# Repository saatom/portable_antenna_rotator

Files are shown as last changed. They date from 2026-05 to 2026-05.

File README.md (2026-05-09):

# Portable Antenna Rotator
Made by two teams as part of our senior design capstone projects for our respective degrees at the University of Alaska Fairbanks
| Mechanical Engineering | Electrical Engineering |
|---|---|
| Alex Armstrong | Nadia Finley |
| Matthew Crisafi-Lurtsema | Isaac Newton |
| [Wyatt Richards](mailto:wr1701@proton.me) | William Payne |

## Overview
This project was made for the Arctic Amateur Radio Club (KL7KC) in Fairbanks, Alaska to enable easy radio communication with satellites and ground-based targets alike with a single, GPS-enabled device with 400+ degrees of azimuth and 180 degrees of elevation control.

The code is intended to be run on a Raspberry Pi 4b with the relevant Python packages installed.
antenna_pic

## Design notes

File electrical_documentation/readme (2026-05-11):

# The electrical_documentation folder holds an interface control document (ICD) and drawing files that describe the electrical connections 
# for the portable antenna rotator.

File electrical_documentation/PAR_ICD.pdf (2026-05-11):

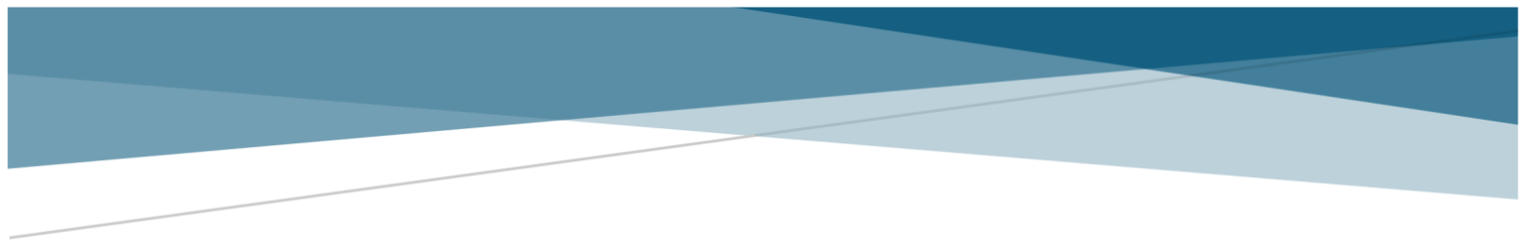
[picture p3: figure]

# PORTABLE ANTENNA ROTATOR (PAR)

## Interface Control Document

Version 1.0
04/29/2026

University of Alaska Fairbanks | EE 482 Senior Design

i
ICD Version 1.0 | Portable Antenna Rotator

## Contents

ii

## Table of Figures

iii

## List of Tables

## 1. Introduction

This ICD describes the relationship between:
- PAR electrical box and the PAR rotator structure.
- PAR electrical box and the external power source.
- Raspberry Pi 4B (RPi) and the connected sensors, motors, touchscreen, and relays.
- PAR and the operator.

This ICD specifies the interface requirements which the participating systems must meet. It describes the concept of operations for the interface, defines the protocols that govern the interchange of data, and identifies the communication paths along which the project team expects signals to flow.
For each interface, the ICD provides the following information:
- A description of the data exchange format and protocol for exchange
- A general description of the interface
- Assumptions where appropriate

## 1.1 Overview

The interface between the electrical box and the rotator structure exists to convey power and control signals between the rotator structure and the electrical box. A 10 ft DSUB cable provides power for the motors, control signals for the motors, I2C signals for the magnetometer / accelerometer, and analog voltages from the potentiometer on the rotator structure.
The interface between the electrical box and the external power source exists to provide a way to power PAR and distribute power to additional equipment. An Anderson power pole bus connected to the outer wall of the electrical box provides a way for the operator to connect a battery. Additional equipment may also be connected to this bus to receive power from the battery.
The interface between the RPi and the connected sensors, motors, touchscreen, and relays exists to provide the RPi with data about the condition of the electrical box and its surroundings, steer the rotator structure in a desired direction, and control indication lights. Dupont connectors link RPi GPIO pins to voltage buses and pin connections on the sensors. The interface between PAR and the operator exists to provide a way for the operator to input data, see RPi operation, manage files, analyze satellite passes, and control the rotator structure.

## 2. Assumptions/Constraints/Risks

It is assumed that the operator will provide their own power through a power pole connection.

## 2.2 Constraints

Connection to the rotator structure must be done with the provided 17 pin DSUB cable. This cable must only be connected to the PAR electrical box to avoid damaging components as the motors will draw significant current.
The power source connected to the power pole bus must have a voltage within 9 – 32 VDC. Whenever voltage from the source degrades below 9 VDC, the system will lose power. The operator should take this into consideration when connecting a battery.

## 3. Interface Overview

## 3.1 Interface Overview

The electrical box-rotator structure interface conveys power and control signals between the electrical box and the rotator structure. The interface is made through a 17-pin, 10 ft DSUB cable. This cable provides 12 VDC power for the elevation servo motor, 5 VDC for the azimuth control feedback potentiometer, and 3 VDC for an accelerometer. Alongside power distribution, the DSUB cable also relays I2C data between the accelerometer and the RPi, analog data from the potentiometer to an analog to digital converter in the electrical box, PWM signals from the RPi to the servo motor, and pulse control signals to the azimuth stepper motor from the stepper motor driver.
The interface between the electrical box and the external power source provides a way to power the Portable Antenna Rotator (PAR) and distribute power to additional equipment. The interface is made through a six-pole, twelve terminal power pole bus that is connected to the outer wall of the electrical box. This bus allows the operator to connect a battery through the power pole connectors. Allowable voltages on this bus are 9 VDC to 32 VDC. Power from the power pole connection is distributed to both the control / operator interface circuitry inside the electrical box as well as to the motors and electrical components on the rotator structure. Additional equipment separate from PAR can be powered from the power pole bus by connecting the equipment in parallel to the battery.

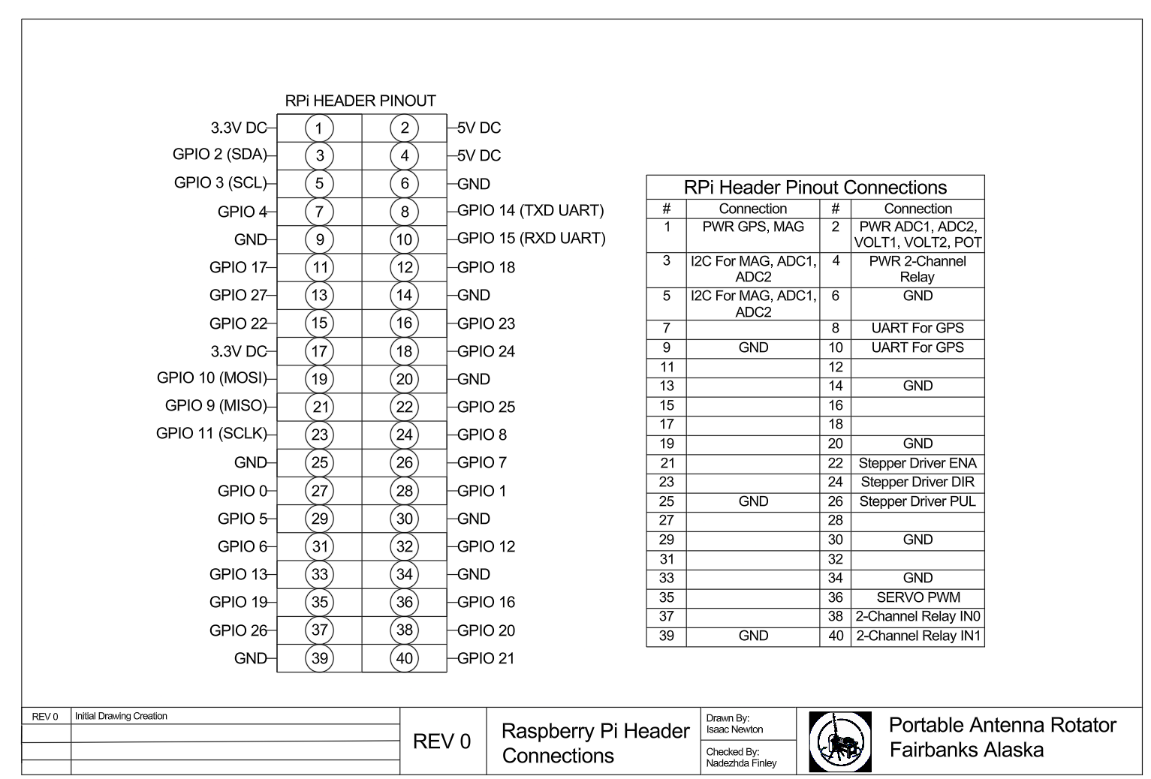
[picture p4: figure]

Figure 1: PAR-004 Design Drawing, RPi Header Diagram

The interface between the RPi and the sensors, motors, touchscreen, and relays provides the RPi a way to perceive information about PAR and its surroundings, control the rotator structure, and communicate system information to the operator. The RPi DSI FPC display port is used to connect the RPi to the touchscreen display, and the RPi 40-pin GPIO is used to connect the RPi to the various peripherals. Figure 1 above shows connections on the RPi GPIO for reference. Signal interfacing protocols on the GPIO include I2C, UART, PWM, and pulse signals written into the Portable Antenna Rotator Router (PARR) program. +3 VDC and +5 VDC power for low current draw sensors are also sourced from the RPi GPIO. Devices connected to the RPi include: two USB extension cables, a 7 inch touchscreen display, two analog to digital converters, two voltage divider “voltmeters”, a GPS, an accelerometer / magnetometer, a servo motor, a stepper motor driver, and a relay for the LED indication lights. Dupont connectors link RPi GPIO pins to voltage buses and pin connections on the sensors.
The interface between PAR and the operator provides a way for the operator to input data, visualize RPi operation, manage files, interact with satellite tracking software, and control the rotator structure. The interface is accomplished through a touch screen, two accessible USB-A ports, a power switch, and an emergency power-off button. The touchscreen provides a way for the operator to interact with the PARR program, communicate with the controller, and steer the rotator structure. The USB-A ports allow the operator to connect a USB storage device, mouse, or keyboard to the RPi for file upload and interfacing. The power switch and emergency power-off button allow the operator to control the flow of power to PAR. The switch connects and disconnects power from the power pole bus to PAR, and the emergency power-off button is a resettable button that disconnects power from the RPi and motors and turns on a green LED light while compressed.

3.1.1 Interface Controls

Table 1: Electrical Box to Rotator Structure Interface Connections
Interface Type | Interface From | Interface To | Description of Interface | Other Information
DSUB Connector | PAR rotator structure | PAR electrical box | Connects 12 VDC power, 5 VDC power, 3 VDC power, stepper motor control signals, PWM signals, I2C signals, and analog potentiometer voltage between the rotator structure and RPi

Table 2: Electrical Box to External Power Source Interface Connections
Interface Type | Interface From | Interface To | Description of Interface | Other Information
9 - 32 VDC power | Power source | Electrical box | Anderson Power Pole Connectors

Table 3: RPi to Sensors, Motors, Touchscreen, and Relay Interface Connections
Interface Type | Interface From | Interface To | Description of Interface | Other Information
RPi GPIO | Board Pin # 1 | Magnetometer, GPS | 3.3 VDC Power
RPi GPIO | Board Pin # 2 | ADC1, ADC2, Voltmeter1, Voltmeter2, Potentiometer | 5 VDC Power

RPi GPIO | Board Pin # 3 | Magnetometer / Accelerometer, ADC1, ADC2 | SDA
RPi GPIO | Board Pin # 4 | 2CH Relay (LED) | 5 VDC Power
RPi GPIO | Board Pin # 5 | Magnetometer / Accelerometer, ADC1, ADC2 | SCL
RPi GPIO | Board Pin # 6 | GND | GND
RPi GPIO | Board Pin # 9 | GND | GND
RPi GPIO | Board Pin # 8 | GPS RX | UART (RPi TX)
RPi GPIO | Board Pin # 10 | GPS TX | UART (RPi RX)
RPi GPIO | Board Pin # 14 | GND | GND
RPi GPIO | Board Pin # 20 | GND | GND
RPi GPIO | Board Pin # 22 | Stepper Motor Driver | Stepper Enable
RPi GPIO | Board Pin # 24 | Stepper Motor Driver | Stepper Direction
RPi GPIO | Board Pin # 25 | GND | GND
RPi GPIO | Board Pin # 26 | Stepper Motor Driver | Stepper Pulse
RPi GPIO | Board Pin # 30 | GND | GND
RPi GPIO | Board Pin # 34 | GND | GND
RPi GPIO | Board Pin # 36 | Servo Motor | PWM Signal
RPi GPIO | Board Pin # 38 | 2CH Relay (LED) | Pulse Signal
RPi GPIO | Board Pin # 39 | GND | GND
RPi GPIO | Board Pin # 40 | 2CH Relay (LED) | Pulse Signal
RPi USB | RPi USB-A | USB Extension Cable
RPi USB | RPi USB-A | USB Extension Cable
RPi Display Port | RPi DSI Display Port | 7 Inch Touchscreen Display | FPC Connector

Figure 2 shows a KiCad schematic for the connections to the RPI GPIO.

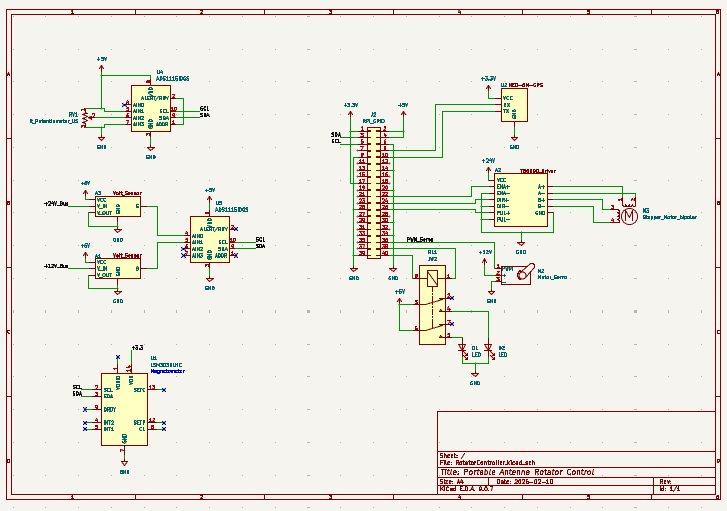
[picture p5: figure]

Figure 2: Portable Antenna Rotator RPi GPIO Connections, KiCad Schematic

Table 4: PAR Electrical Box to Operator Interface Connections
Interface Type | Interface From | Interface To | Description of Interface | Other Information
Touchscreen | Touchscreen | Operator | Provides the Operator with Visual Feedback and Tactile Control of the RPi
USB Port 1 | RPi USB Port | External USB-A Connector
USB Port 2 | RPi USB Port | External USB-A Connector
Power Switch | Power Line | Operator | Allows Operator to Control Power Flow to PAR
Emergency Power-off Button | Further Along the Power Line | Operator | Allows Operator to Remove and Restore Power to the RPi and Motors

## 3.2 Functional Allocation

The function of the electrical box is to act as the control and power distribution center of PAR. The DSUB interface between the electrical box and the rotator structure supports the function of the electrical box by transmitting power and signals to components on the rotator structure. To engage the DSUB interface, the operator must uncoil the 10 ft cable from stowed position and plug the cable into the DSUB terminal on the electrical box.
The function of the electrical box to external power source interface is to provide a way for the operator to connect power to the PAR system and other devices connected to the power pole bus. To connect a power source to the power pole bus, the operator must connect cables terminated with Anderson power pole connectors to the power pole bus on the box. To power external devices off of the power pole bus, the operator must plug in devices to the bus using cables terminated with Anderson power pole connectors.

The function of the RPi to sensors and motors interface is to provide the RPi with a means of sensing its surroundings and to control the rotator structure. There is nothing that the operator must do to engage this interface for system operation.
The function of the PAR to operator interface is to provide a way for the operator to engage with the PAR system. To power on PAR, the operator will need to disengage the emergency power-off button and flip the power switch to the “ON” position. To navigate files, apps, and the PARR program, the operator must either utilize the touchscreen function of the display or connect a mouse and keyboard to the USB ports.

## Appendix A: Record of Changes

This interface control document should be kept in a folder with other PAR related documentation to keep a record of interface connections and purposes for system maintenance and updates to system design.

Table 5: Record of Changes

Version Number | Date | Author | Description of Change
1.1 | 04/29/2026 | Nadezhda Finley | First version; no changes
<X.X> | <MM/DD/YYYY> | | <Description of Change>
<X.X> | <MM/DD/YYYY> | | <Description of Change>
<X.X> | <MM/DD/YYYY> | | <Description of Change>

## Appendix B: Glossary

Table 6: Glossary
Term | Acronym | Definition
Portable Antenna Rotator | PAR | The portable antenna rotator is the antenna rotator system whose interfaces are described in the present document. PAR consists of an electrical box and a rotator structure.
Portable Antenna Rotator Router | PARR | Portable Antenna Rotator Router is the Python software program written to control PAR.

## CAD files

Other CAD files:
electrical_documentation/electrical_drawings/Rpi_Header.dwg
electrical_documentation/electrical_drawings/One_Line.dwg
electrical_documentation/electrical_drawings/Electrical_Box.dwg
electrical_documentation/electrical_drawings/DC-Schematic_2.dwg
electrical_documentation/electrical_drawings/D-Sub Connector.dwg

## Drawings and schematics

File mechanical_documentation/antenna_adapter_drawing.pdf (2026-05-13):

# 98.15 mm

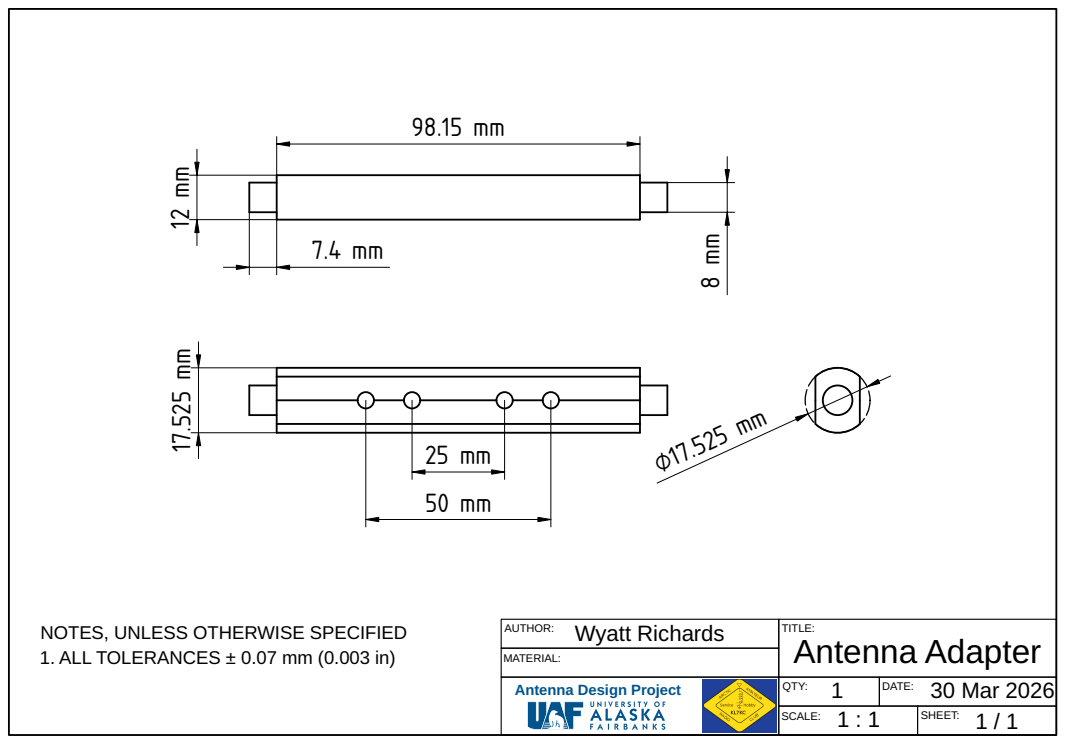
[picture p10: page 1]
AUTHOR:; DATE:; SHEET:; SCALE:; TITLE:; Wyatt Richards; 30 Mar 2026; 1. ALL TOLERANCES ± 0.07 mm (0.003 in); Antenna Adapter; QTY:

NOTES, UNLESS OTHERWISE SPECIFIED

MATERIAL:
Antenna Design Project

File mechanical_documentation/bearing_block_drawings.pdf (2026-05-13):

0.188 "

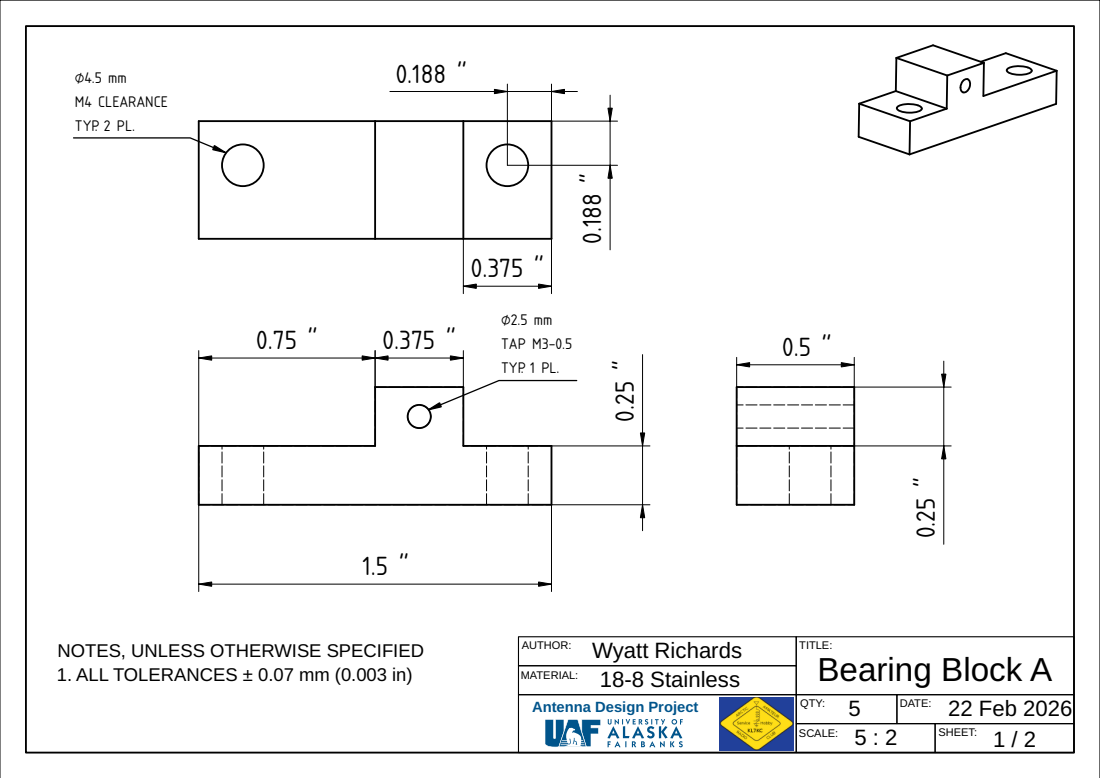
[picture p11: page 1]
AUTHOR:; DATE:; SHEET:; SCALE:; TITLE:; MATERIAL:; Wyatt Richards 18-8 Stainless; 22 Feb 2026; 1. ALL TOLERANCES ± 0.07 mm (0.003 in); Bearing Block A; QTY:; TAP M3-0.5; TYP. 1 PL.; M4 CLEARANCE; TYP. 2 PL.

NOTES, UNLESS OTHERWISE SPECIFIED

Antenna Design Project

⌀0.118 "

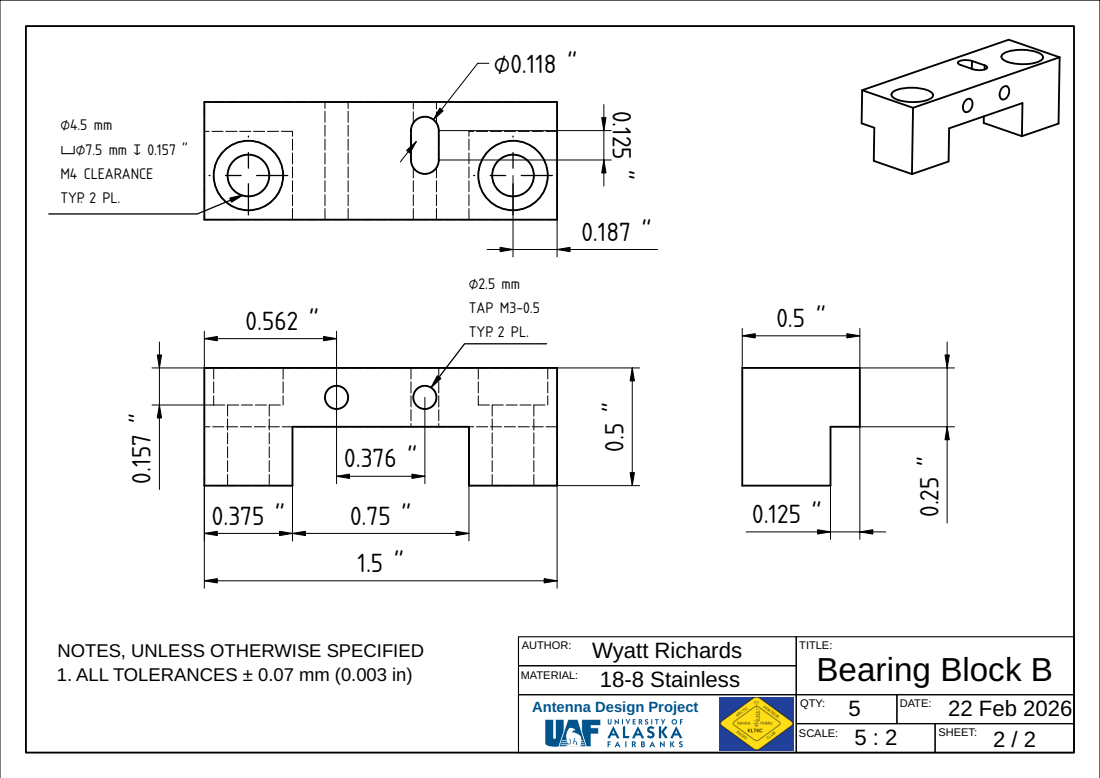
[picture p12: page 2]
AUTHOR:; DATE:; SHEET:; SCALE:; TITLE:; MATERIAL:; Wyatt Richards 18-8 Stainless; 22 Feb 2026; 1. ALL TOLERANCES ± 0.07 mm (0.003 in); Bearing Block B; QTY:; TAP M3-0.5; TYP. 2 PL.; M4 CLEARANCE

NOTES, UNLESS OTHERWISE SPECIFIED

Antenna Design Project

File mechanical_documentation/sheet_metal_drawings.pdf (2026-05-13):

205.41 mm

## 38.1 mm ⌀4.5 mm

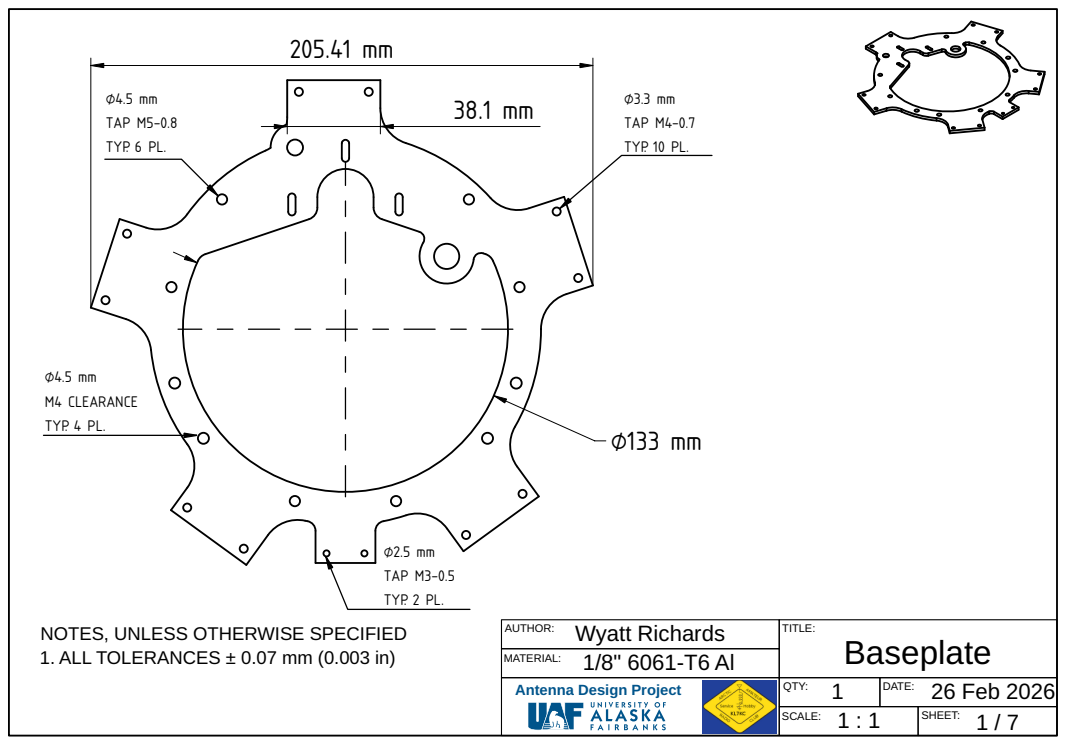
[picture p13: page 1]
AUTHOR:; DATE:; SHEET:; SCALE:; TITLE:; MATERIAL:; Wyatt Richards 1/8" 6061-T6 Al; 26 Feb 2026; 1. ALL TOLERANCES ± 0.07 mm (0.003 in); Baseplate; QTY:; TAP M5-0.8; TYP. 6 PL.; TAP M4-0.7; TYP. 10 PL.; M4 CLEARANCE; TYP. 4 PL.; TAP M3-0.5; TYP. 2 PL.

NOTES, UNLESS OTHERWISE SPECIFIED

Antenna Design Project

138 mm

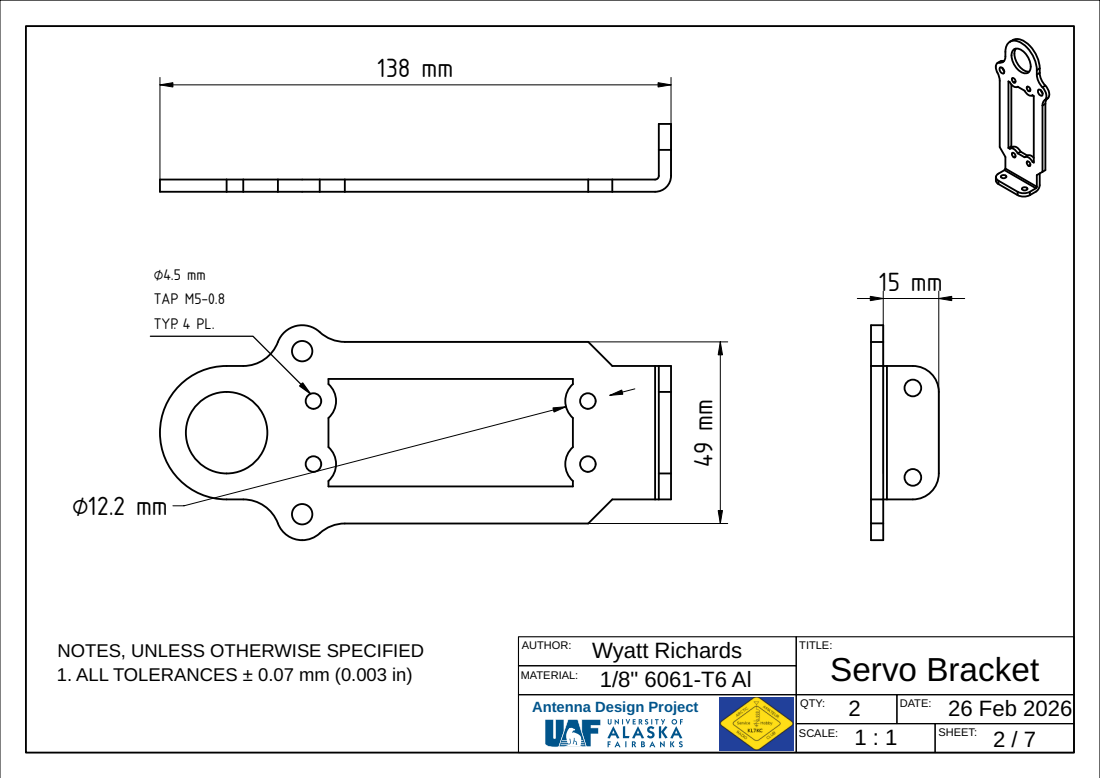
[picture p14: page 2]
AUTHOR:; DATE:; TITLE:; MATERIAL:; Wyatt Richards 1/8" 6061-T6 Al; 26 Feb 2026; 1. ALL TOLERANCES ± 0.07 mm (0.003 in); Servo Bracket; QTY:; TAP M5-0.8; TYP. 4 PL.

NOTES, UNLESS OTHERWISE SPECIFIED

Antenna Design Project

## R14 mm

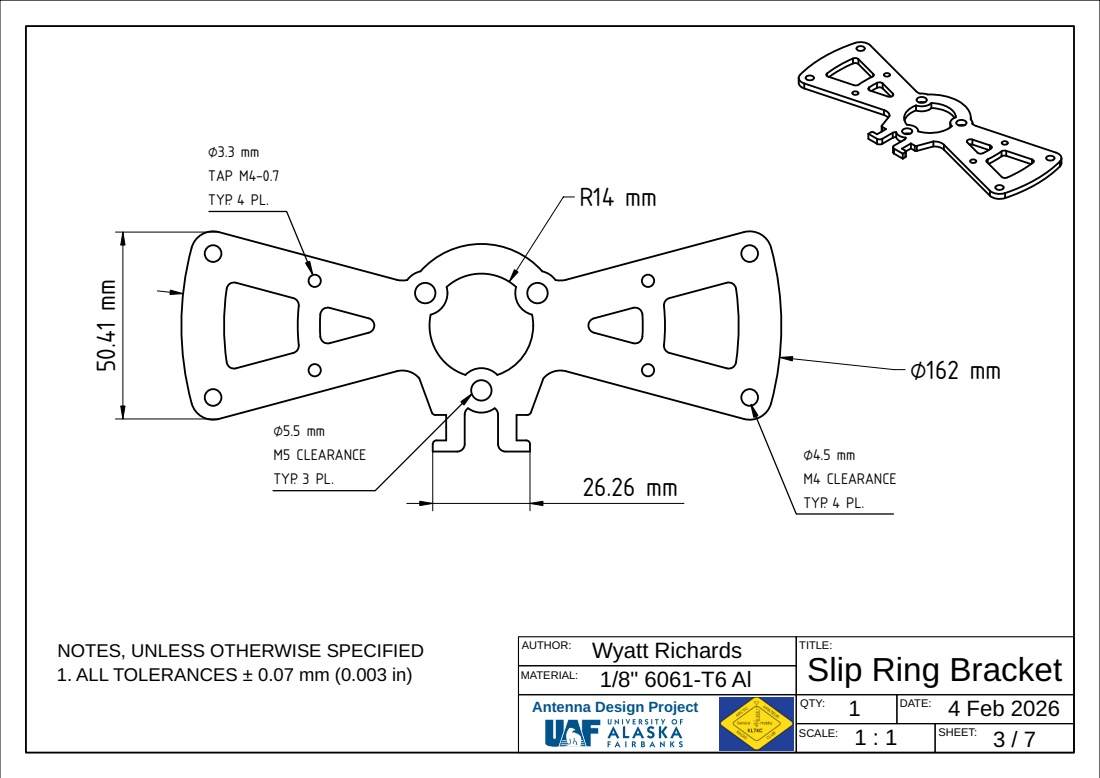
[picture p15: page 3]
AUTHOR:; DATE:; TITLE:; MATERIAL:; Wyatt Richards 1/8" 6061-T6 Al; 4 Feb 2026; 1. ALL TOLERANCES ± 0.07 mm (0.003 in); Slip Ring Bracket; QTY:; TAP M4-0.7; TYP. 4 PL.; M4 CLEARANCE; M5 CLEARANCE; TYP. 3 PL.

NOTES, UNLESS OTHERWISE SPECIFIED

Antenna Design Project

59.11 mm

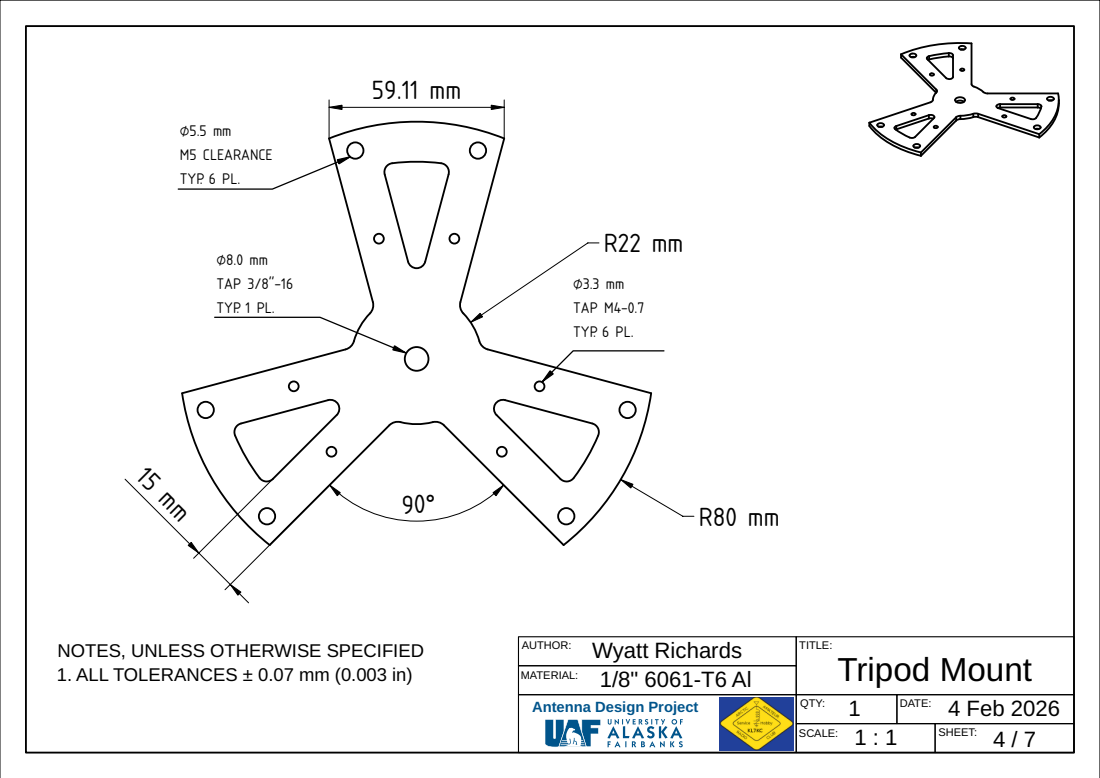
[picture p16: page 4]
AUTHOR:; DATE:; TITLE:; MATERIAL:; Wyatt Richards 1/8" 6061-T6 Al; 4 Feb 2026; 1. ALL TOLERANCES ± 0.07 mm (0.003 in); Tripod Mount; QTY:; TAP M4-0.7; TYP. 6 PL.; M5 CLEARANCE; TAP 3/8"-16; TYP. 1 PL.

NOTES, UNLESS OTHERWISE SPECIFIED

Antenna Design Project

⌀3.3 mm

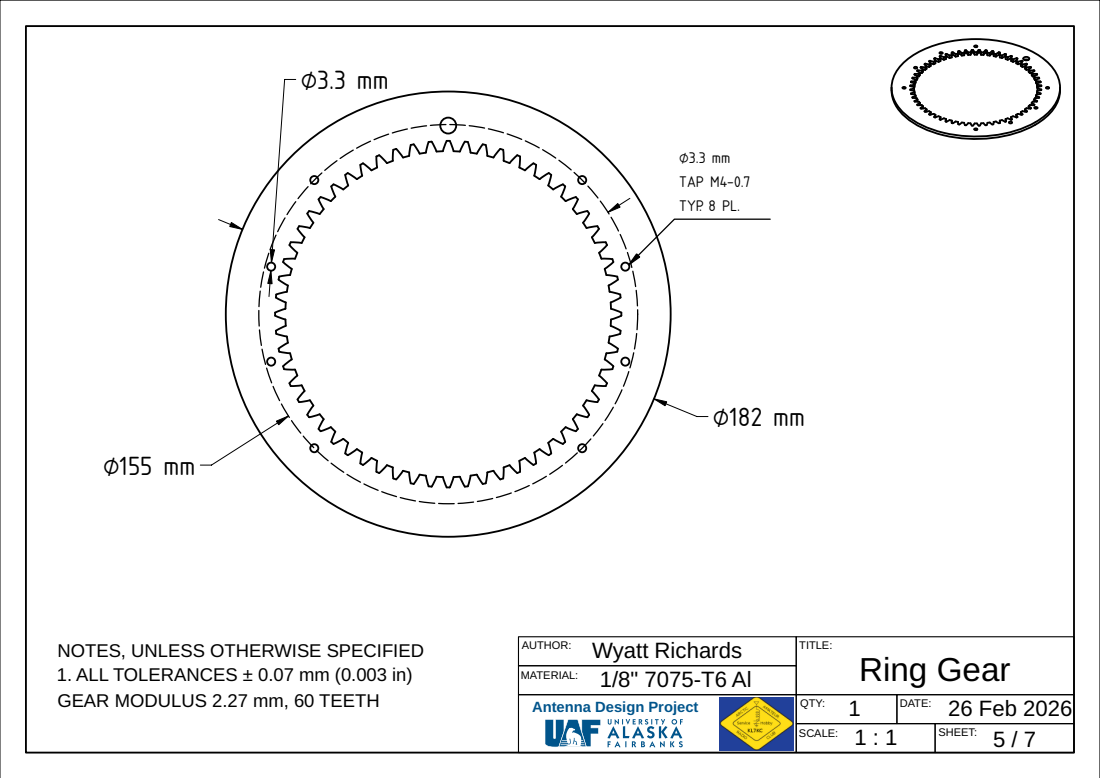
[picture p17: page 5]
AUTHOR:; DATE:; TITLE:; MATERIAL:; Wyatt Richards 1/8" 7075-T6 Al; 26 Feb 2026; 1. ALL TOLERANCES ± 0.07 mm (0.003 in); Ring Gear; GEAR MODULUS 2.27 mm, 60 TEETH; QTY:; TAP M4-0.7; TYP. 8 PL.

NOTES, UNLESS OTHERWISE SPECIFIED

Antenna Design Project

⌀17.52 mm

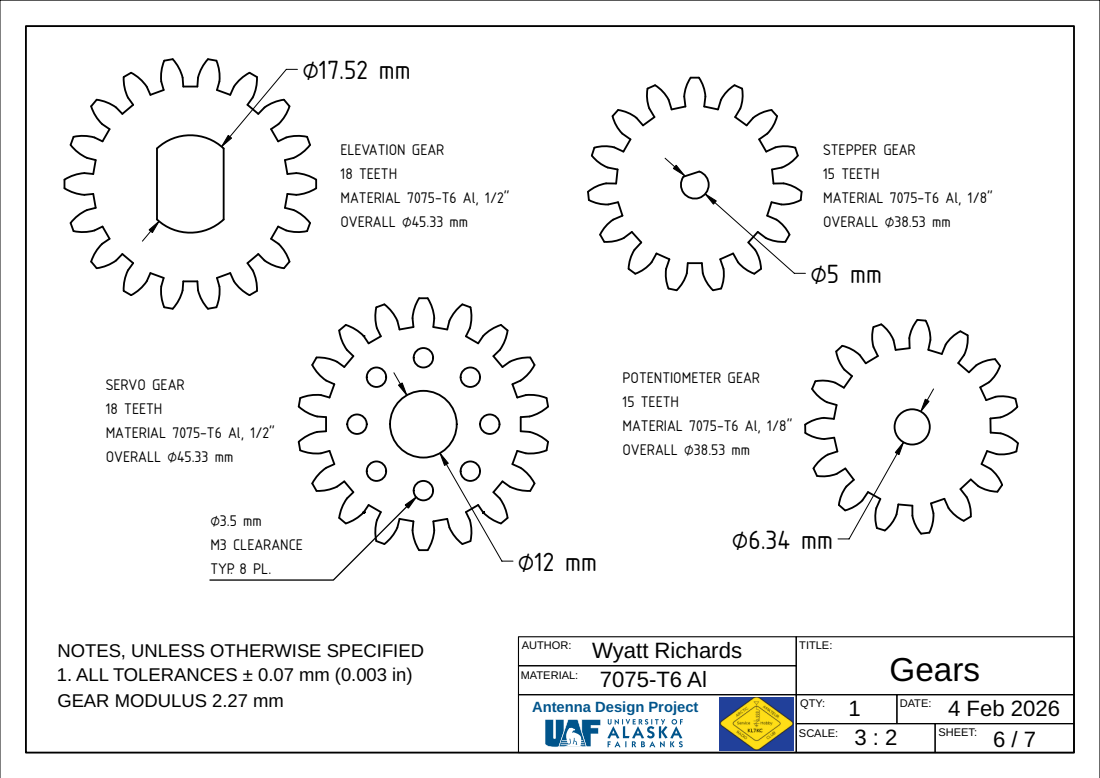
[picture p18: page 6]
AUTHOR:; DATE:; TITLE:; MATERIAL:; Wyatt Richards 7075-T6 Al; 4 Feb 2026; 1. ALL TOLERANCES ± 0.07 mm (0.003 in); Gears; GEAR MODULUS 2.27 mm; QTY:; ELEVATION GEAR; 18 TEETH; MATERIAL 7075-T6 Al, 1/2"; OVERALL ⌀45.33 mm; SERVO GEAR; STEPPER GEAR; 15 TEETH; MATERIAL 7075-T6 Al, 1/8"; OVERALL ⌀38.53 mm; POTENTIOMETER GEAR; M3 CLEARANCE; TYP. 8 PL.

NOTES, UNLESS OTHERWISE SPECIFIED

Antenna Design Project

3.3 mm

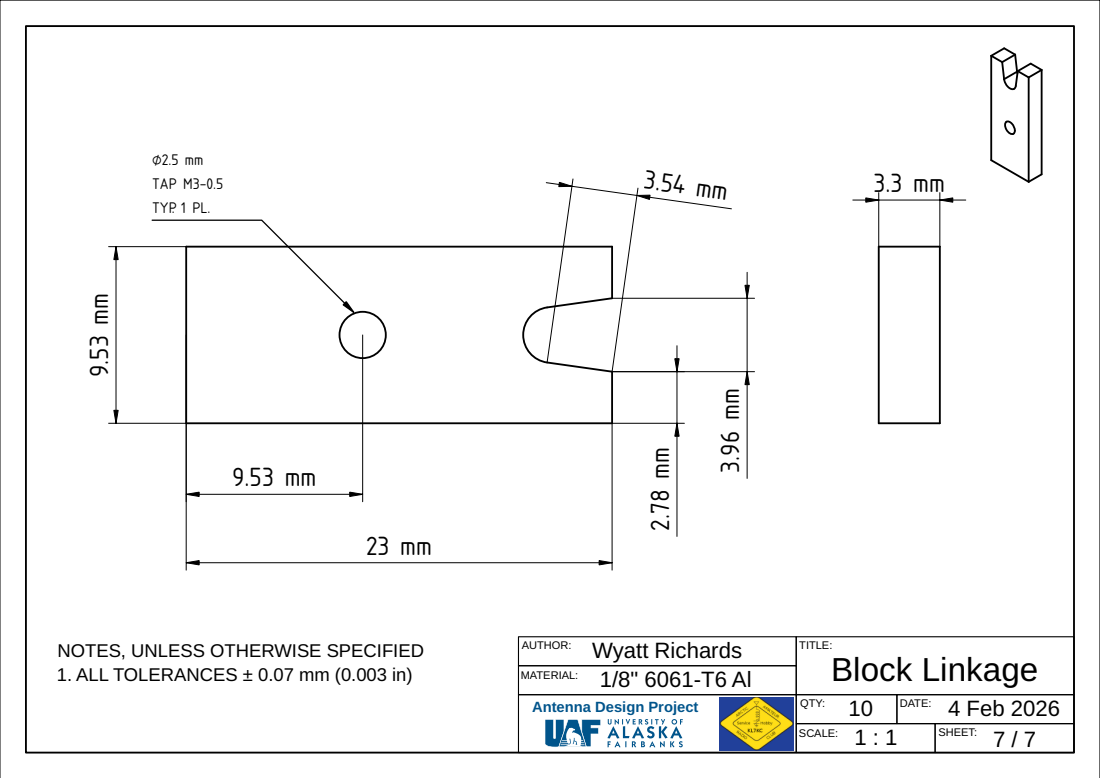
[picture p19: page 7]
AUTHOR:; DATE:; TITLE:; MATERIAL:; Wyatt Richards 1/8" 6061-T6 Al; 4 Feb 2026; 1. ALL TOLERANCES ± 0.07 mm (0.003 in); Block Linkage; QTY:; TAP M3-0.5; TYP. 1 PL.

NOTES, UNLESS OTHERWISE SPECIFIED

Antenna Design Project

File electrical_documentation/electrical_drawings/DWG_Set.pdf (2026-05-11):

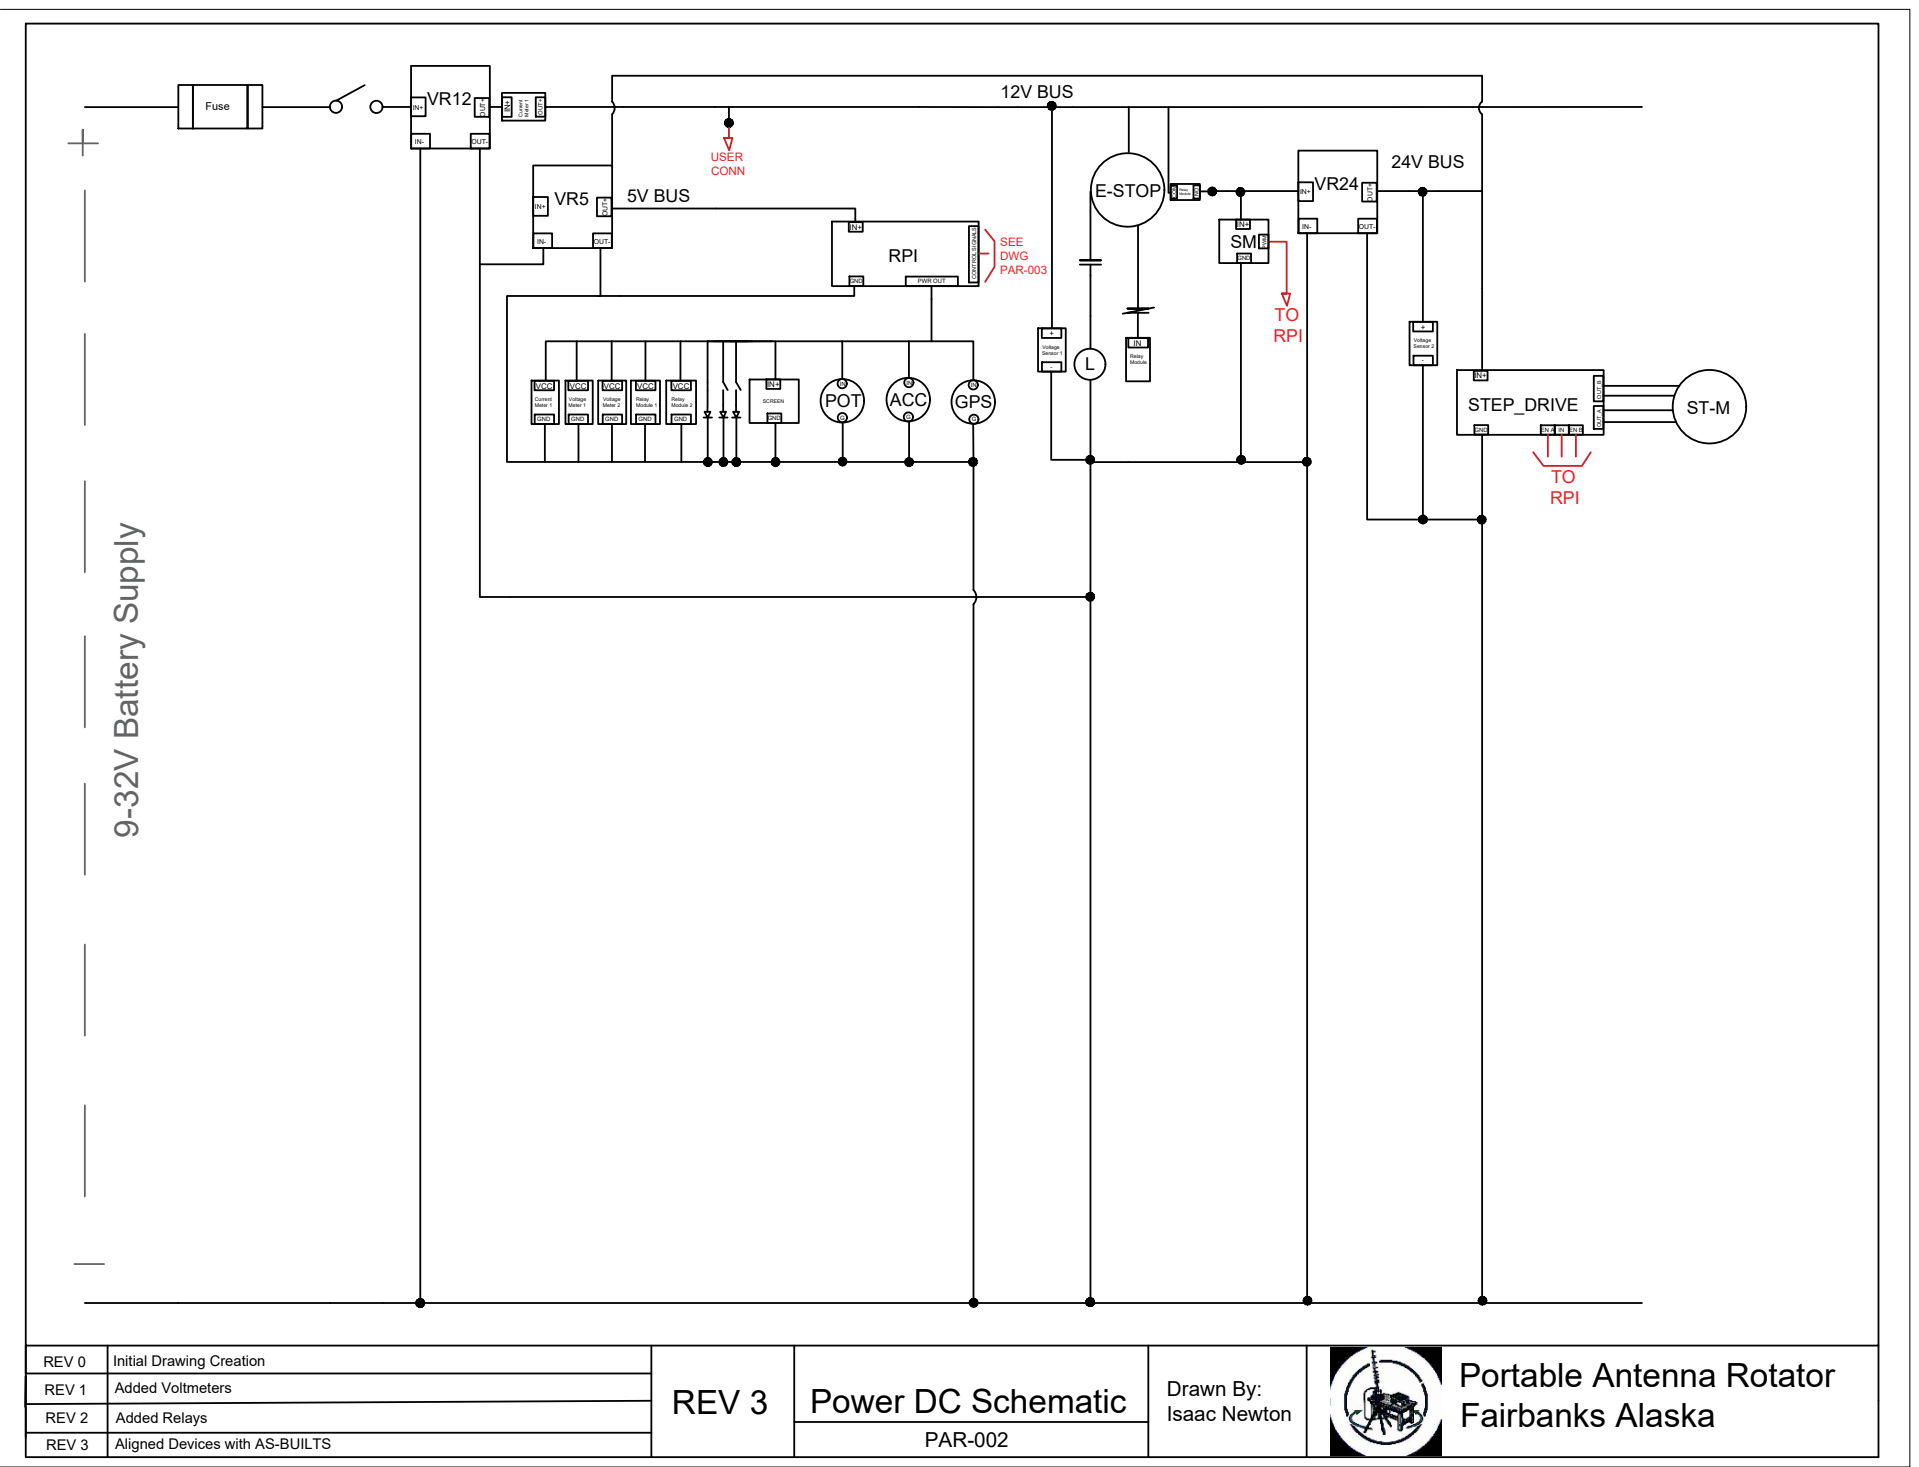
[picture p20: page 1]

9-32V Battery Supply Fuse IN+IN- OUT+ OUT- VR12 12V BUS E-STOP L SMIN+ GND IN+IN- OUT+ OUT- VR24 24V BUS

Current Meter 1 OUT+ Portable Antenna Rotator Fairbanks Alaska Drawn By: REV 3 Power DC Schematic Isaac Newton REV 0 REV 1 REV 2 REV 3 Initial Drawing Creation Added Voltmeters Added Relays Aligned Devices with AS-BUILTS PAR-002

CONTROL SIGNALS PWR OUT SCREEN POT ACC GPS IN+ GND G G G IN IN IN SEE DWG PAR-003 USER CONN VCC GND Voltage Meter 1 VCC GND Voltage Meter 2 +- Voltage Sensor 1 +- Voltage Sensor 2 INRelay Module

COMRelay Module NO VCC GND Relay Module 1 VCC GND Relay Module 2 VCC GND Current Meter 1

OUT_B OUT_AST-M EN A IN EN B TORPI IN+IN- OUT+ OUT- VR5 5V BUS RPI IN+ GND

PWM TORPI STEP_DRIVE IN+ GND

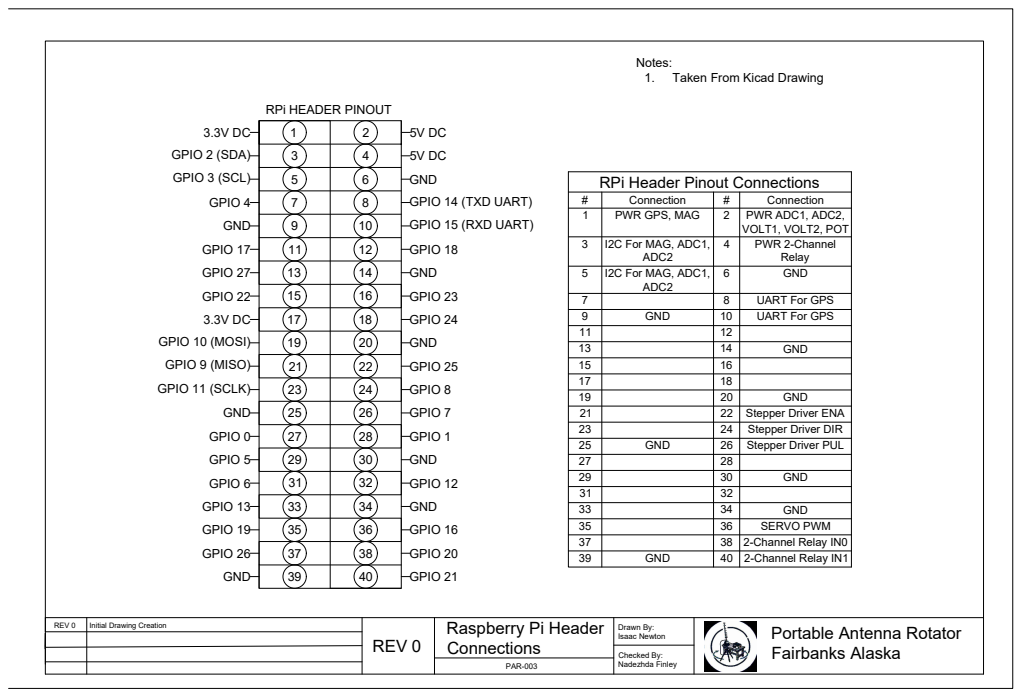
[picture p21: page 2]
Portable Antenna Rotator Fairbanks Alaska Drawn By: Isaac Newton Checked By: Nadezhda Finley Raspberry Pi Header REV 0; Connections REV 0; Initial Drawing Creation; 5V DC 5V DC GND GPIO 14 (TXD UART) GPIO 15 (RXD UART) GPIO 18 GND GPIO 23 GPIO 24 GND GPIO 25 GPIO 8 GPIO 7 GPIO 1 GND GPIO 12 GND GPIO 16 GPIO 20 GPIO 21 3.3V DC GPIO 2 (SDA) GPIO 3 (SCL) GPIO 4 GND GPIO 17 GPIO 27 GPIO 22 3.3V DC GPIO 10 (MOSI) GPIO 9 (MISO) GPIO 11 (SCLK) GND GPIO 0 GPIO 5 GPIO 6 GPIO 13 GPIO 19 GPIO 26 GND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

2 1:SERVO PWR 2:SERVO GND 3:MAG PWR 4:MAG SDA 5:MAG SDL; 6:MAG GND 7:POT + 8:POT SLIDE 9:POT - 10:SERVO SIG 11:SPARE 12:A+ 13:A- 14:B+ 15:B-; 16:SPARE 17:SPARE 9; 1 1:SERVO PWR 2:SERVO GND 3:MAG PWR 4:MAG SDA 5:MAG SDL; 16:SPARE 17:SPARE FEMALE SIDE REAR VIEW MALE SIDE REAR VIEW; Portable Antenna Rotator Fairbanks Alaska Drawn By: Isaac Newton D-Sub Layout REV 1 REV 0 REV 1; Initial Drawing Creation Added Servo Signal Connection; PAR-004

LEFT SIDE

CONTROL SIGNALS 3.3V PWR OUT Screen IN+ GND GPSGIN IN: AE-OUT+, AE-OUT- GND: AD-GND, AM-GND, ADC1-GND, ADC2-GND 3.3V: ACC-IN 5V: AD-VCC, AM-IN+, AM-IN+,ADC1-VCC,ADC2-VCC,POT-IN SDA: ADC1-SDA,ADC2-SDA,ACC-SDA SCL: ADC1-SCL,ADC2-SCL,ACC-SCL TX: RX: IN+: AK-5V GND: AK-GND AB-OUT+ IN: ACC-IN, L1-IN G: AK-GND AE-IN+ POTGIN IN: AK-5V SLIDE: ADC2-A2 G: AK-GND --AG-- OUT-VR24 OUT+ IN- IN+: T1-8 IN-:T2-5 OUT+: T1-9 OUT-: T2-7 IN+ AA Current meter 1 IN+ VCC IN+: OUT+: VCC: SIG: GND: OUT+ SIG GND AB AD Volt meter 1 + VCC +: T1-5 -: T2-4 VCC: AD-VCC, AG-VCC SIG: ADC1-A1 GND: AK-GND - SIG GND AF Volt meter 2 VCC +: T1-9 -: T2-7 VCC: AF-VCC, AH-VCC SIG: ADC1-A0 GND: AK-GND SIG GND AG Relay 1 VCC NO1: L2-IN COM1: L1-IN NC1: NO2: L3-IN COM2: AH-COM1 NC2: VCC: AG-VCC, AI-DC+ IN1: IN2: GND: AK-GND IN1 IN2 AH Relay 2 DC+ NO: COM: T1-8 NC: DC+: AH-VCC DC-: AK-GND IN: AC-NC2 DC- IN AI AE + - NO COM NC NO COM NC NO COM NC K1 K2 GND AC-NO1 AB-IN+ VM 1 ESTOP ESTOP 24V IN NO2 NC2 ESTOP NO1 NC1 AJ AL N/A 24V OUT STEP-DR AK AM L2 IN: AH-NO1 GND: L1-GND, L3-GND L3 IN: AH-NO2 GND: L2-GND, T2-3 L4 IN: AC-NO2 GND: T2-4 AE-IN- L3-GND L4-GND AB-IN- AA-OUT- AB-OUT- AL-GND BOX LEVEL 2 P1-7 ACCGIN IN: AK-3.3V G: AK-GND Portable Antenna Rotator Fairbanks Alaska Drawn By: REV 1 Electrical Box Wiring Isaac Newton REV 0 REV 1 Initial Drawing Creation Added Component plate ADC1 A0 VCC: AK-5V GND: AK-GND SDA: AK-SDA SCL: AK-SCL ADDR: A0: AG-SIG A1: AF-SIG A2: A3: A1 A2 ADC1 A3 VCCGND SDA SCL ADDR ADC1 A0 VCC: AK-5V GND: AK-GND SDA: AK-SDA SCL: AK-SCL ADDR: AD2-SDA A0: A1: POT-IN A2: POT-SLIDE A3: POT-GND A1 A2 ADC2 A3 VCCGND SDA SCL ADDR Notes: 1. This circuit is the proposed design 2. Real wiring powers AE from 24V terminal to avoid unintentional resets PAR-006

RIGHT SIDE HINGE WALL BOTTOM WALL T1 123456 SW-2 AA-OUT+ AA-IN+ N/A N/A 789101112 1 Fuse 2 FU1 FU1-1: BAT+ FU1-2: SW-1 BAT BAT + : FU1-1 BAT - : T2-1 P1 123456 T1-7 CUST CONN T2-9 SW1 2 SW-1: FU1-2 SW-2: T1-1 IN+ OUT- VR5 IN- OUT+ IN+: T1-4 IN-: T2-2 OUT+: AK-IN OUT-: AK-IN IN+ OUT- VR12 IN- OUT+ IN+: T1-2 IN-: T2-1 OUT+: T1-3 OUT-: T2-6 12V REG 12V REG 12V PWR 5V IN CUST CONN CUST CONN CUST CONN CUST CONN CUST CONN CUST CONN CUST CONN CUST CONN CUST CONN T2 123456 BAT- AA-IN- AK-GND 789101112 -AJ-GND, AF-- PWR PWR PWR PWR 789101112 ACNO1: T1-6 NC1: T1-7 NO2: L4-IN NC2: AI-IN AF-+ AI-COM AC-NC1 AJ-IN+ P1-1 AG-+ Servo Motor IN+ GNDPWM EXTERNAL CONNECTIONS IN+: T1-8 GND: T2-4 PWM: RPi pin STEP_DRIVER IN+ GND

OUT_B OUT_A EN A IN EN B IN+: T1-10 GND: T2-8 OUT_A+: ST-M-A+ OUT_A-: ST-M-A- OUT_B+: ST-M-B+ OUT_B-: ST-M-B- EN_A: IN: EN_B: AI-NC AL-IN+ ST-M A+: AL_OUTA+ A-: AL_OUTA- B+: AL_OUTB+ B-: AL_OUTB- Raspberry PI 4B INGND

BOX BOTTOM LEVEL 1
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

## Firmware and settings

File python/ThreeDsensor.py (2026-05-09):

# Distributed with a free-will license.
# Use it any way you want, profit or free, provided it fits in the licenses of its associated works.
# LSM303DLHC
# This code is designed to work with the LSM303DLHC_I2CS I2C Mini Module available from ControlEverything.com.
# https://www.controleverything.com/products

import smbus2
import time

# Get I2C bus
bus = smbus2.SMBus(1)

# LSM303DLHC Accl address, 0x19(25)
# Select control register1, 0x20(32)
#		0x27(39)	Acceleration data rate = 10Hz, Power ON, X, Y, Z axis enabled
bus.write_byte_data(0x19, 0x20, 0x27)
# LSM303DLHC Accl address, 0x19(25)
# Select control register4, 0x23(35)
#		0x00(00)	Continuos update, Full scale selection = +/-2g,
bus.write_byte_data(0x19, 0x23, 0x00)

time.sleep(0.5)

# LSM303DLHC Mag address, 0x1E(30)
# Select MR register, 0x02(02)
#		0x00(00)	Continous conversion mode
bus.write_byte_data(0x1E, 0x02, 0x00)
# LSM303DLHC Mag address, 0x1E(30)
# Select CRA register, 0x00(00)
#		0x10(16)	Temperatuer disabled, Data output rate = 15Hz
bus.write_byte_data(0x1E, 0x00, 0x10)
# LSM303DLHC Mag address, 0x1E(30)
# Select CRB register, 0x01(01)
#		0x20(32)	Gain setting = +/- 1.3g
bus.write_byte_data(0x1E, 0x01, 0x20)

time.sleep(0.5)


def readAccl():
    # LSM303DLHC Accl address, 0x19(25)
    # Read data back from 0x28(40), 2 bytes
    # X-Axis Accl LSB, X-Axis Accl MSB
    try:
        data0 = bus.read_byte_data(0x19, 0x28)
        data1 = bus.read_byte_data(0x19, 0x29)

    # Convert the data
        xAccl = data1 * 256 + data0
        if xAccl > 32767 :
            xAccl -= 65536
    except:
        xAccl = 65536
            
        # LSM303DLHC Accl address, 0x19(25)
        # Read data back from 0x2A(42), 2 bytes
        # Y-Axis Accl LSB, Y-Axis Accl MSB
    try:
        data0 = bus.read_byte_data(0x19, 0x2A)
        data1 = bus.read_byte_data(0x19, 0x2B)
    
        # Convert the data
        yAccl = data1 * 256 + data0
        if yAccl > 32767 :
            yAccl -= 65536
    except:
        yAccl = 65536
        
        # LSM303DLHC Accl address, 0x19(25)
        # Read data back from 0x2C(44), 2 bytes
        # Z-Axis Accl LSB, Z-Axis Accl MSB
    try:
        data0 = bus.read_byte_data(0x19, 0x2C)
        data1 = bus.read_byte_data(0x19, 0x2D)

        # Convert the data
        zAccl = data1 * 256 + data0
        if zAccl > 32767 :
            zAccl -= 65536
    except:
        zAccl = 65536
        
    xAccl = (xAccl/65536)*4
    yAccl = (yAccl/65536)*4
    zAccl = (zAccl/65536)*4
    
    return xAccl, yAccl, zAccl

def readMag():
    # LSM303DLHC Mag address, 0x1E(30)
    # Read data back from 0x03(03), 2 bytes
    # X-Axis Mag MSB, X-Axis Mag LSB
    try:
        data0 = bus.read_byte_data(0x1E, 0x03)
        data1 = bus.read_byte_data(0x1E, 0x04)

        # Convert the data
        xMag = data0 * 256 + data1
        if xMag > 32767 :
            xMag -= 65536
    except:
        xMag = 65536
        
        # LSM303DLHC Mag address, 0x1E(30)
        # Read data back from 0x05(05), 2 bytes
        # Y-Axis Mag MSB, Y-Axis Mag LSB
    try:
        data0 = bus.read_byte_data(0x1E, 0x07)
        data1 = bus.read_byte_data(0x1E, 0x08)
    
        # Convert the data
        yMag = data0 * 256 + data1
        if yMag > 32767 :
            yMag -= 65536
    except:
        yMag = 65536

        # LSM303DLHC Mag address, 0x1E(30)
        # Read data back from 0x07(07), 2 bytes
        # Z-Axis Mag MSB, Z-Axis Mag LSB
    try:
        data0 = bus.read_byte_data(0x1E, 0x05)
        data1 = bus.read_byte_data(0x1E, 0x06)
    
        # Convert the data
        zMag = data0 * 256 + data1
        if zMag > 32767 :
            zMag -= 65536
    except:
        zMag = 65536    
            
    xMag = (xMag/65536)*2.6
    yMag = (yMag/65536)*2.6
    zMag = (zMag/65536)*2.6
    
    return xMag, yMag, zMag

def IsEnabled():
    try:
        t1 = readMag()
        t2 = readAccl()
        print("3DSensor | Working")
        return True
    except:
        print("3DSensor | Nope, doesn't work")
        return False

# Output data to screen
#Accl = readAccl()
#Mag = readMag()
#print(f"Accelerometer | ({Accl[0]:.4f} X, {Accl[1]:.4f} Y, {Accl[2]:.4f} Z)")
#print(f"Magnetometer | ({Mag[0]:.4f} X, {Mag[1]:.4f} Y, {Mag[2]:.4f} Z)")
IsEnabled()

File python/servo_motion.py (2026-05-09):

#Servo motor test code
# import RPi.GPIO as GPIO
from gpiozero.pins.pigpio import PiGPIOFactory
from gpiozero import Servo
import time
import subprocess
subprocess.run(['sudo', '/home/aarc_portable_rotator/rot-env/lib/python3.13/site-packages/pigpio-79/pigpiod'])

factory = PiGPIOFactory()
SetAngleVal = 90
pwmMax=2.5
pwmMin=0.5
frequency=50
period=1/frequency*1000
myGPIO=16
MoveOn = False


servo = Servo(myGPIO, initial_value=None, min_pulse_width=pwmMin/1000, max_pulse_width=pwmMax/1000, pin_factory=factory) # intiail value set to none to prevent max force angle changes
# Max force angle changes still exist. This bugfix didnt work :)

GlobalAngle = 90
AngleOffset = 0
with open("ServoSaveState.txt", "r") as file:
    lines = file.readlines()
    GlobalAngle = float(lines[0])
    AngleOffset = float(lines[1])       

# servo takes in values between -1 and 1 for full range of motion
# Input from gpredict will be in degrees: 0 to 90
def sign(x):
    return (x>0)-(x<0)

def move(angle):
    global GlobalAngle
    global AngleOffset
    # Servo motor ranges 270 deg.
    # On the rotator, 22.5deg is level with horizon.
    # 5 degrees added to make the rotator level
    # (angle/90*5) added to compensate for an odd non-linearity
    angle1 = (float(angle) + 22.5 + 5) + (float(angle)/90*5)
    angle2 = (angle1-135)/(135)
    #print(angle)
    servo.value = angle2
    with open("ServoSaveState.txt", "w") as file:
        file.write(str(angle)+"\n")
        file.write(str(AngleOffset))
        GlobalAngle = angle
        
    
def SetAngle(angle):
    global SetAngleVal
    SetAngleVal = angle
    print("Servo Setpoint |", SetAngleVal)

def MoveSlow(DegreesPerSecond = 10):
    global GlobalAngle
    global SetAngleVal
    global MoveOn
    AngleDifference = SetAngleVal - GlobalAngle
    TimeStep = 1e-3
    Tolerance = True
    while MoveOn & Tolerance:
        TimeStart = time.perf_counter()
        #print("TimeStep -", TimeStep)
        Increment = sign(AngleDifference)*min(abs(AngleDifference),DegreesPerSecond*TimeStep)
        #print("Setpoint -", Increment+GlobalAngle, Increment)
        move(Increment+GlobalAngle)
        AngleDifference = SetAngleVal - GlobalAngle
        Tolerance = not(ToleranceCheck(1e-1))
        TimeStop = time.perf_counter()
        TimeStep = TimeStop - TimeStart

def Start():
    global MoveOn
    MoveOn = True
    print("Motor Started")
            
def Stop():
    global MoveOn
    MoveOn = False
    print("Motor Stopped")
    
def ToleranceCheck(Tolerance):
    global SetAngleVal
    global GlobalAngle
    #print("Tolerance Values -", SetAngleVal, GlobalAngle)
    return Tolerance>abs(SetAngleVal - GlobalAngle)

def GetAngle():
    global GlobalAngle
    return GlobalAngle

def OffsetAngle(angle):
    global AngleOffset
    AngleOffset = angle
    
def GetOffsetAngle():
    global AngleOffset
    return AngleOffset
    
